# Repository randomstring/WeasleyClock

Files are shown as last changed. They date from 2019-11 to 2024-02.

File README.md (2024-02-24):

# Weasley Clock

Build a working physical [Weasley
Clock](https://harrypotter.fandom.com/wiki/Weasley_Clock) from Harry
Potter.

Photo album of the build: <https://photos.app.goo.gl/7yxiuzpsFReUh5Yy5>

Details of the build can be found in my [Build Log](BuildLog.md).

## Design

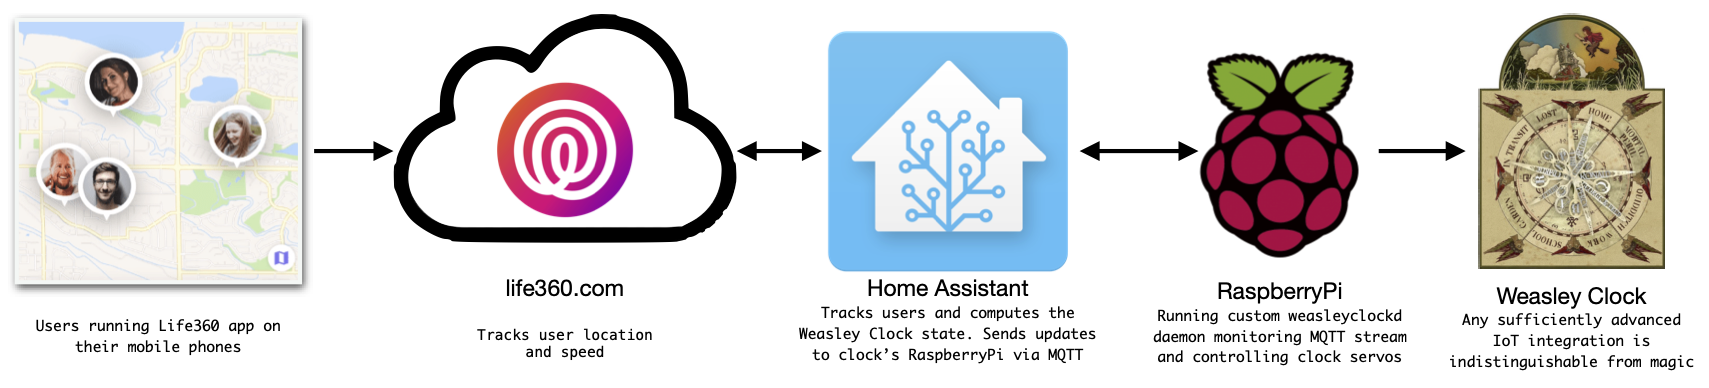
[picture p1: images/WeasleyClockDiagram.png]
Weasley Clock Flow Diagram


1. Track location of family members using the Apple iCloud integration
   in HomeAssistant. This service allows for real-time
   updates of each family member's location and speed. HomeAssistant allows
   for naming of arbitrary geo-fenced areas. This is used for labeling
   locations like school and work. I might switch over to using Traccar at some point to get
   better reporting on movement. The initial implementation used life360, but
   they locked out any external access to their API, breaking the HomeAssistant
   integration. 

2. Use [Home Assistant](https://www.home-assistant.io/) as a clearing
   house for family member location and movement within and around
   home. Home assistant is hosted on a Raspberry Pi
   running [Hass.io](https://www.home-assistant.io/hassio/).

3. Custom Home Assistant rules calculate the Weasley Clock state for
   each family member. Each state is visible from the Home Assistant
   dashboard. Changes in clock state are transmitted to the physical
   clock using the MQTT protocol over the network.

4. [Custom software](https://github.com/randomstring/weasleyclockd)
   running on a Raspberry Pi monitoring the MQTT message stream for
   changes in clock state and updating the physical clock hands to
   match. This software also adds some flare to hand movement. For
   example, the placement of the hand within each clock face sector
   will be determined by the person's distance from home. This way you
   can tell if someone is far or near to home at a glance. You might
   even be able to notice the progress of the person's clock hand
   progressing towards home.

5. A physical clock with four hands. The clock is mounted into an old
   grandfather clock. The face of the clock is divided into eight
   nearly equal sectors. Each sector has a location/situations
   label. These labels are: Home, Mortal Peril, Quidditch, Work,
   School, Garden, In Transit, and Lost.

6. The next phase will be to reuse the chimes that came with the
   original clock. The chimes can alert to noteworthy changes in the
   clock's state, for example, announcing someone's arrival back
   home. The current plan is to use a stepper motor to drive the
   existing chime mechanism.

## Clock Face and Meaning of Sectors

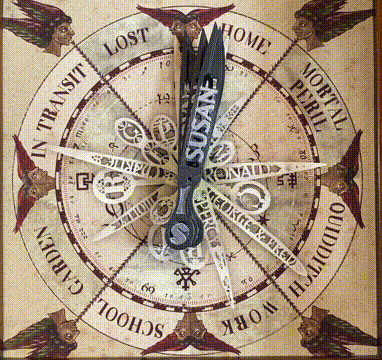
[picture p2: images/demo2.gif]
Weasley Clock Demo 2
Weasley Clock Demo 3 

What each sector of the clock face means:

* **Home** The home state is triggered by the Home Assistant Apple iCloud
  integration. I have a defined geo-fenced area, when we are inside
  that region, we are considered home. I also use the Home Assistant
  Unifi integration to identify when members of the family are
  connected to the home WiFi network. Additionally, I can identify
  which WiFi access points (APs) they are connected to. This provides
  some granularity as to where they on the property. The system can
  tell if someone is in the shop, in the main house, or outside in the
  garden. I use the clockwise half of the Home sector to indicate
  someone is in the main house and the counter-clockwise half to
  indicate someone is in the shop.

* **Lost** This is a catch-all state for when someone is stationary,
  not at home, and is not at one of the named locations of School or
  Work. The clock hand varies its location within the sector
  depending on how far from home they are. The closer to home, the
  closer the hand inches towards the Home sector. The position within
  the Lost sector varies on a logarithmic scale to give a finer
  grain detail when closer to home.

* **In Transit** This indicates the family member is on the move.

* **Garden** This sector is triggered when connecting to the WiFi
  access point outside, near the garden.

* **School** Triggered when at a location labeled as "school."

* **Work** Triggered when at a location labeled as "work."

* **Quidditch** Triggered when someone is bicycling. I have this
  triggered in two ways. First, by a complex set of rules about low
  speed movement, faster than walking and slower than
  driving. Secondly, I detect when someone is currently active on
  [Zwift](https://zwift.com/), an VR indoor cycling app.

* **Mortal Peril** This is triggered if the tracker measures someone's
  speed as greater than 75mph. With teenagers on the verge of driving
  age, I will be watching this one closely.

## Case Design

I decided to reuse an old grandfather/grandmother clock instead of
building a new case. I got lucky and found a perfect case at a thrift
shop. The clock was a petite grandfather clock, sometimes referred to
as a grandmother clock. Not as imposing and difficult to move as a
full sized grandfather clock. I needed the dimensions of the face to
match the artwork I have and the depth of the case needed to hold the
servos and new clockwork.

## Clock Hands

Hands are 3D printed with the name of each family member on the hands,
just like in the Harry Potter movies. The bottom of each hand has the
person's initial. Hands are painted for better contrast and to give an
aged appearance.

I spent a long time trying to figure out how to secure the hands to
the brass tube axles. I considered clamping hubs (too bulky), collets
(metal connectors traditional clock hands use), glue, and hot glue
(this works well). In the end, by making the holes in the 3D printed
hands strategical smaller, I was able to expand the holes with a file
so that they just fit. They were tight enough to be secure. I did
remove too much material from one of the hands and resorted to glue
(E-6000) to keep it in place.

Here are the [fonts](fonts/Fonts.md) I evaluated for use on the hands.

## Related Projects and Inspiration

Over the course of this build I spent a fair amount of time
researching how others have attempted to build a Weasley Clock. The
most complete and authentic build I've found is by [Printable
Props](https://www.instagram.com/printableprops/).

-   <https://www.allderhallows.com/>
-   <https://hunterjm.github.io/location-clock/>
-   <https://github.com/WhereslyClock/MyWhereslyClock>
-   <http://www.themagicclock.com/>
-   <https://printableprops.jimdo.com/en/harry-potter/weasley-clock/>
-   <https://www.instructables.com/id/Build-Your-Own-Weasley-Location-Clock/>
-   <https://www.facebook.com/PrintableProps/>
-   <https://www.instagram.com/printableprops/>
-   <https://fourierinformationsir.wordpress.com/2015/11/09/weasley-clock-update/>
-   <https://twitter.com/wbtourlondon/status/765398939910627328>
-   <https://www.youtube.com/playlist?list=PL86twtxo_L9TMY4A5TcG2nJcsyFx2CWhb>
-   <https://magicclock.de/>
-   <http://www.brettoliver.org.uk/Longcase_Clock/Longcase_Clock.htm>
-   <https://www.youtube.com/watch?v=NH0jhxouQM8>
-   <https://www.youtube.com/watch?v=WJ2PBmOW_Rc>
-   <http://www.thisispete.com/work/prototyping/weather_clock/>
-   <https://imgur.com/gallery/wX98fOc>
-   <https://www.reddit.com/r/homeassistant/comments/ts0y6a/got_round_to_converting_my_weasley_clock_to_be/>

## Artwork

I looked around on the internet and there are two styles of faces for
the Weasley clock that appear in the Harry Potter movies. The first
style comes up more often, and it is easier to replicate. It also has
some sectors like "Prison" that I hope to never need.

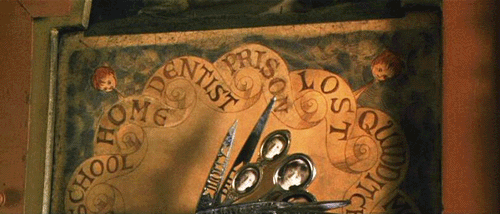
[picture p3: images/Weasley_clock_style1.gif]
Weasley Clock Style 1


I prefer the second style.

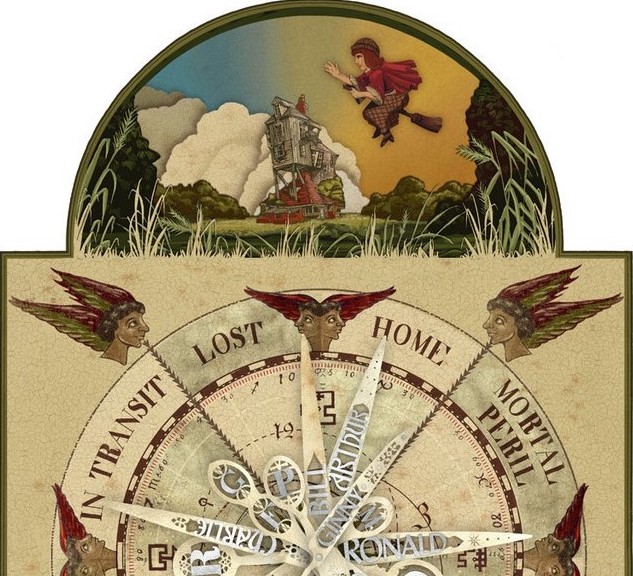
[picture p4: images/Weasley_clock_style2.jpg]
Weasley Clock Style 1


As luck would have it, [Minalima](https://minalima.com/), the artists
of this style, sell officially licensed [posters of the Weasley
Clock](https://minalima.com/product/the-weasley-family-clock/). This
was well worth the money for the poster as I didn't have to create the
artwork myself and this *is* the artwork from the Harry Potter movie.

## Chimes

The grandmother/grandfather clock came with a set of chimes. I plan to
integrate them once I have the clock mechanism finished. I started a new project to research and document this build: [Weasley Chimes](https://github.com/randomstring/WeasleyChimes/).

## Home Assistant

I am using [Home Assistant](<https://www.home-assistant.io/>) for
tracking and transmitting the location of my family members. To do
this I am using the [Apple iCloud
integration](<https://www.home-assistant.io/integrations/icloud/>) for
detailed location tracking. For tracking finer locations around the
house I am using the [Unifi
integration](<https://www.home-assistant.io/integrations/unifi>) to
monitor which WiFi access point each family member is closest to.

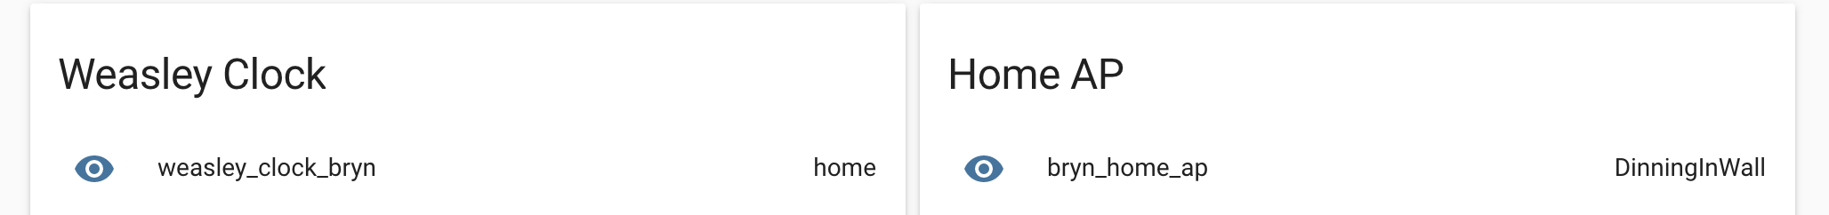
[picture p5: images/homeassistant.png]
Home Assistant Weasley Clock


I'm including example Home Assistant YAML configuration code creating
a Weasley Clock sensor. This sensor will track a given user's Weasley
Clock states:  home, garden, school, work, intransit, mortalperil, lost, error.

Example Home Assistant configurations can be found in the
homeassistant directory. 
 * [automations.yaml](homeassistant/automations.yaml)
 * [sensors.yaml](homeassistant/sensors.yaml)

## Software

I need a daemon running on the Raspberry Pi that controls the clock
servos. For this I
wrote [weasleyclockd](https://github.com/randomstring/weasleyclockd)
that monitors the MQTT messages from Home Assistant and manages the
physical clock movement.

## CAD Models of Parts

Most of the parts from ServoCity.com have CAD models that can be found
here: <https://www.servocity.com/step-files>

CAD model of the HS-785HB Servo can be found here:
<https://grabcad.com/library/servo-motor-hitec-hs-785hb-1>

Custom CAD files for the clock supports and hands are in the
[CAD](CAD) sub-directory. 

The CAD for the clockworks support structures were created by my
father-in-law, Ron. He also handled all the 3D printing for this
project.

My son, Alex, did the CAD for the clock hands, and generated a CAD
rendering of the clockworks. Complete [CAD renderings of the clockworks
and hands are on GrabCad.com](https://grabcad.com/library/weasley-clock-2).

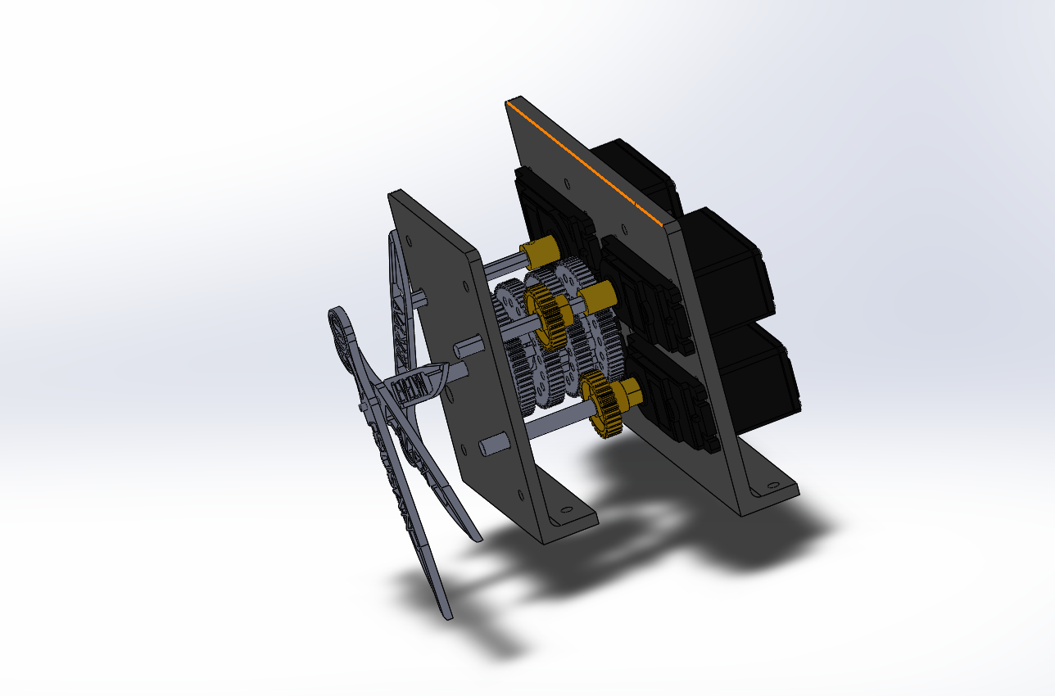
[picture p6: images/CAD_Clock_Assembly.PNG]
Cad View

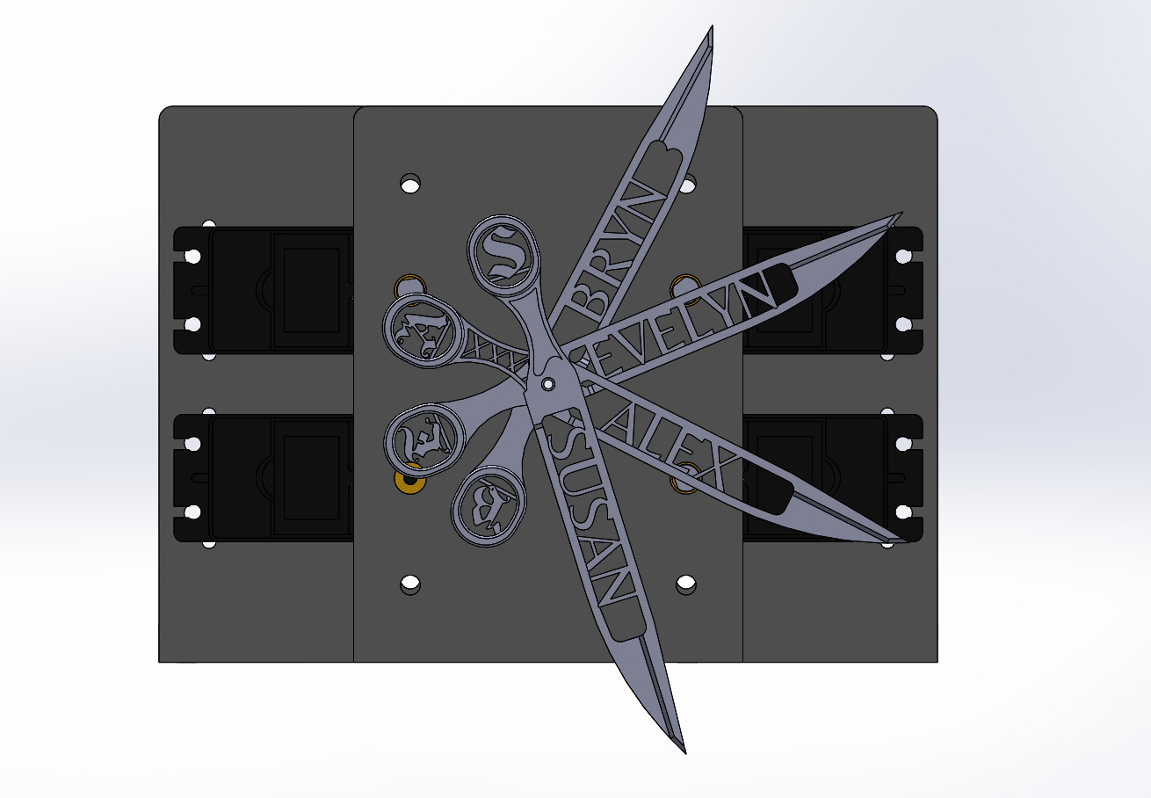
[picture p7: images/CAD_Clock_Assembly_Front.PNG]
CAD Front View


## Mounting poster to plywood

I used 3M Super 77 Spray Adhesive for mounting the clock face artwork. 

I had considered using [Mod
Podge](https://www.amazon.com/Mod-Podge-CS11303-Waterbase-Sealer/dp/B0009ILH8C/)
and went so far as experiment mounting some other posters to plywood
using Mod Podge. 

3M Super 77 leaves the face surface smoother, and doesn't require
coating the front of the art to get good adhesion. Super 77 sets up
really quickly, so watch some videos on how to use it and get a buddy
to help keep the poster straight as you lay it down.

# Shopping list

## Raspberry Pi

-   standard set of Raspberry pi requirements. Pi, power supply, SD card, case

## Servo Hat

-   Raspberry Pi servo hat: <https://www.adafruit.com/product/2327>
    -   requires soldering
-   Servo power, one of:
    -   5V 2A should be enough if motors aren't overloaded simultaneously <https://www.adafruit.com/product/276>
    -   5V 4A to hedge bets, or if you run more servos <https://www.adafruit.com/product/1466>

## Shopping list from Servo City

<table border="2" cellspacing="0" cellpadding="6" rules="groups" frame="hsides">

<colgroup>
<col  class="right" />

<col  class="left" />

<col  class="right" />
</colgroup>
<thead>
<tr>
<th scope="col" class="right">Count</th>
<th scope="col" class="left">Description</th>
<th scope="col" class="right">SKU</th>
</tr>
</thead>

<tbody>
<tr>
<td class="right">4</td>
<td class="left">HS-785HB SERVO</td>
<td class="right">33785S</td>
</tr>

<tr>
<td class="right">3</td>
<td class="left">32T, 0.250" (1/4) Bore 32P Shaft Mount Pinion Gear</td>
<td class="right">615254</td>
</tr>

<tr>
<td class="right">1</td>
<td class="left">32P, 32 Tooth, 24T C1 Spline Servo Mount Gear (Metal)</td>
<td class="right">615290</td>
</tr>

<tr>
<td class="right">3</td>
<td class="left">C1 SPLINE SERVO TO 1/4" SHAFT COUPLER (SET SCREW)</td>
<td class="right">525134</td>
</tr>

<tr>
<td class="right">3</td>
<td class="left">0.250" (1/4") X 2.50" (2-1/2") STAINLESS STEEL D-SHAFTING</td>
<td class="right">634074</td>
</tr>

<tr>
<td class="right">4</td>
<td class="left">32 Pitch, 64 Tooth (.50" Bore) Aluminum Hub Gear</td>
<td class="right">615194</td>
</tr>

<tr>
<td class="right">2</td>
<td class="left">6mm (0.770") Clamping Hub</td>
<td class="right">545616</td>
</tr>

<tr>
<td class="right">2</td>
<td class="left">5mm (0.770") Clamping Hub</td>
<td class="right">545612</td>
</tr>

<tr>
<td class="right">2</td>
<td class="left">4MM (0.770") Clamping Hub</td>
<td class="right">545608</td>
</tr>

<tr>
<td class="right">2</td>
<td class="left">3MM (0.770") Clamping Hub</td>
<td class="right">545604</td>
</tr>
</tbody>
</table>

## Shopping list from Hobbylinc

-   <https://www.hobbylinc.com/htm/k+s/k+s9821.htm>
-   NOTE: checked items are a good set for a 4 hand clock. Theoretically
    possible to create a 6 hand clock with all of the sizes. However,
    servocity doesn't sell clamping hubs for size 2mm and 7mm.
-   parts:
    -   [ ] 2mm x 300mm Round Brass Tube .45mm Wall (4) k+s9820 Item # K+S9820
    -   [X] 3mm x 300mm Round Brass Tube .45mm Wall (4) k+s9821 Item # K+S9821
    -   [X] 4mm x 300mm Round Brass Tube .45mm Wall (3) k+s9822 Item # K+S9822
    -   [X] 5mm x 300mm Round Brass Tube .45mm Wall (3) k+s9823 Item # K+S9823
    -   [X] 6mm x 300mm Round Brass Tube .45mm Wall (2) k+s9824 Item # K+S9824
    -   [ ] 7mm x 300mm Round Brass Tube .45mm Wall (2) k+s9825 Item # K+S9825

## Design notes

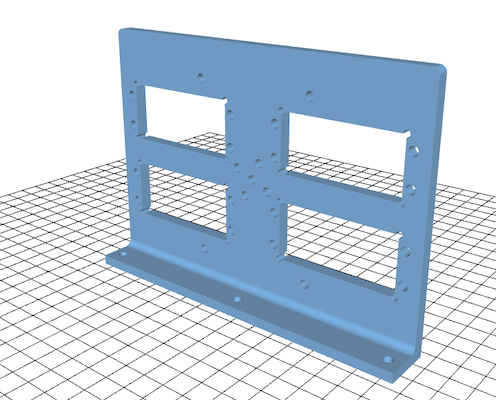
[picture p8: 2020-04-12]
images/CAD_servo_support.png

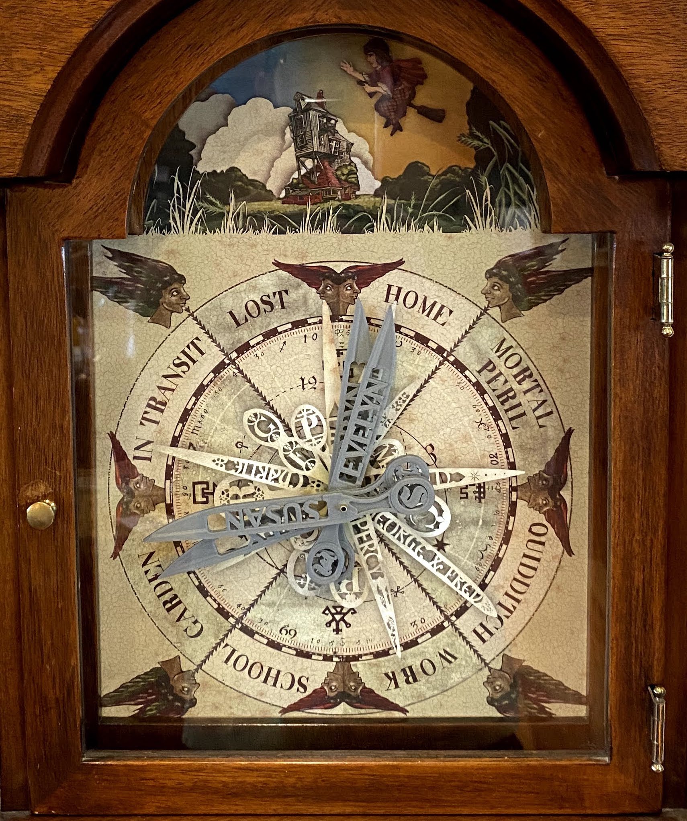
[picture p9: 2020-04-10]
images/WeasleyClockFace.jpeg

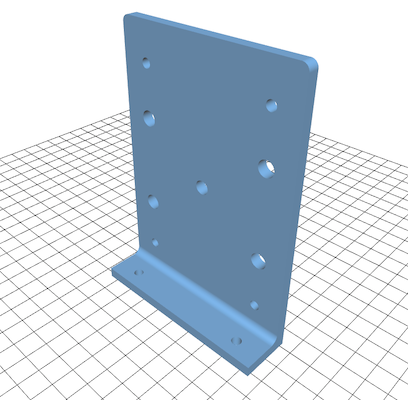
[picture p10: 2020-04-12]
images/CAD_shaft_support.png

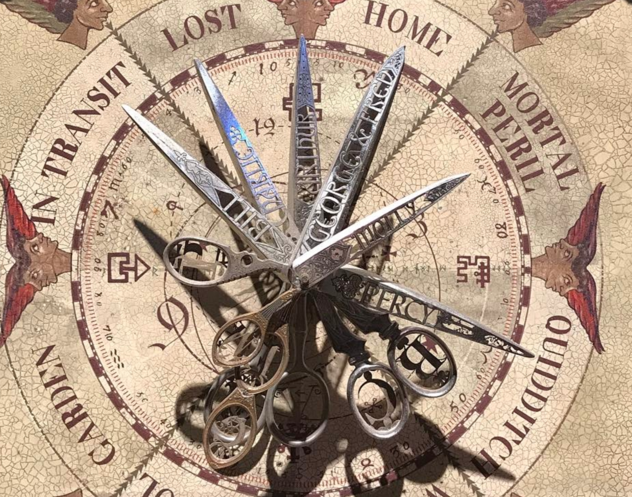
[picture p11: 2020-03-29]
images/ClockHands.png

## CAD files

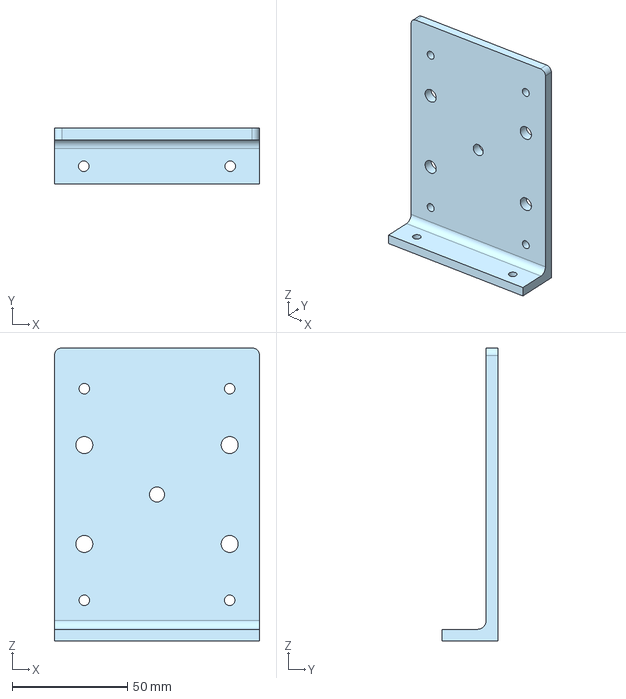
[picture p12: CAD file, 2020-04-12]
CAD/Clock_Shaft_Support.step
88.9 x 24.1 x 127.0 mm

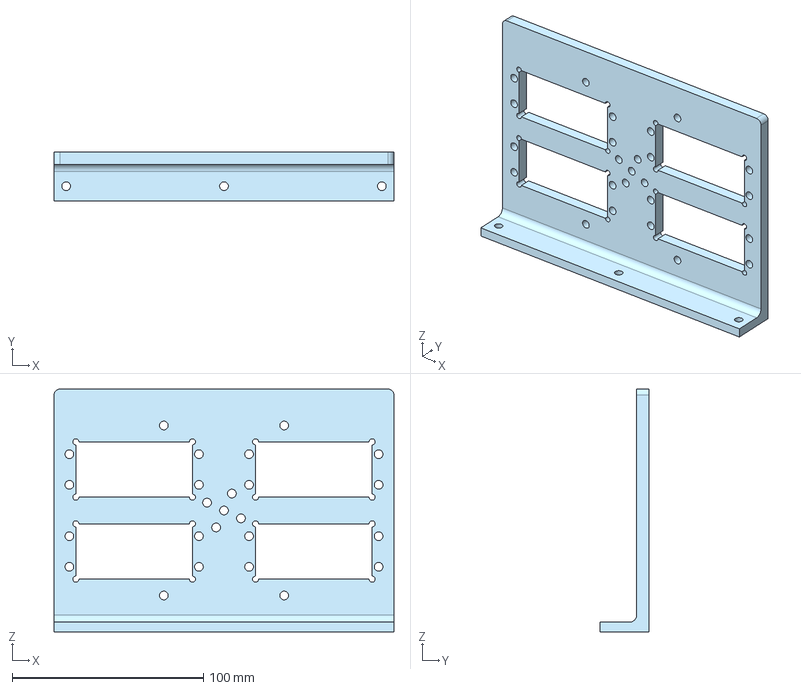
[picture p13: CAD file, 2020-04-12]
CAD/Clock_Servo_Support.step
177.8 x 25.4 x 127.0 mm

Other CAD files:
CAD/Clock_Servo_Support.stl
CAD/Clock_Shaft_Support.stl

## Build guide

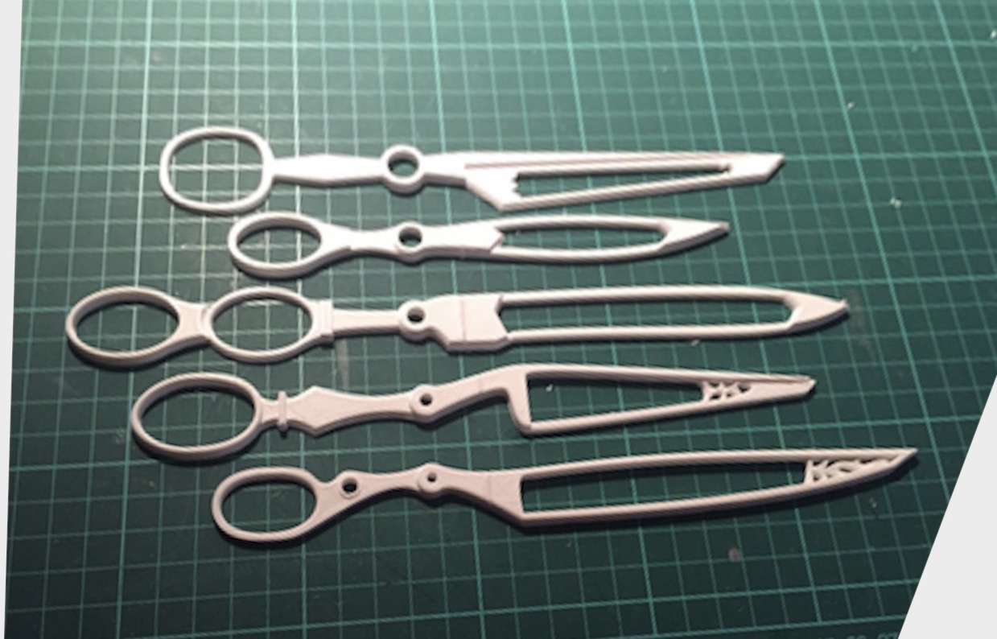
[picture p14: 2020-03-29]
images/PrintableProps_Hands.jpg

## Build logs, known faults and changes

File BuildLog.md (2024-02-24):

# Build Log

I started this log after getting the Weasley Clock feature complete. I
should have started from the beginning. Entries prior to April 2020
are written retrospectively.

## TODO: Build/Code

* create code/algorithm to reliably detect when people are bicycling for the Quidditch state
* better document Zwift integration, post example home assistant configuration

## Why Home Assistant?

I started using [Home Assistant](https://www.home-assistant.io/) when
I was looking at home automation choices. What started this was my
purchase from [Konnected](https://konnected.io/), a system that
converts an old wired alarm system to a modern IoT integration.

Home Assistant is open source and strives to keep all control local
(and private) to your home network.

After over a year of tinkering with Home Assistant, I feel like I've
only scratched the surface of what it's capable of.

I published [example configuration
templates](https://github.com/randomstring/WeasleyClock/tree/master/homeassistant)
for integrating into Home Assistant.

## Why Life360?

I tried the Home Assistant Apple iCloud integration first. The iCloud
API does not seem to be a fully supported and endorsed API. The Home
Assistant integration broke for me at least twice. Once when Apple
changed some details in their authentication.

The Life360 integration has been quite stable and has features
designed around tracking family members. I also managed to get buy-in
from all my family members to use it. Which makes all of this possible. 

Another point is that it works on both iPhones and Android phones.

Life360 allows for setting up several geo-fenced regions and giving
them labels. For instance I have a geo-fence region for each school.
Home Assistant also has this feature, so this can be done in Home
Assistant just using the latitude and longitude provided by Life360.

## Why MQTT?

MQTT is fairly easy to use, can generate arbitrary messages (I use
JSON for the payload), and has extensive support in Home Assistant.

Using python the [Paho MQTT](https://pypi.org/project/paho-mqtt/)
module.

I implemented the MQTT the Weasley Clock Server/Client in a stand
alone repo called
[weasleyclockd](https://github.com/randomstring/weasleyclockd).

The other obvious choice would have been to use an HTTP and RESTful
API. I haven't ruled out adding one. 

## Monolithic Approach

Alternatively, I could have just implemented a direct integration with
Life360 on the Raspberry Pi. This would have taken the form of a
single daemon running on the Weasley Clock that would poll Life360 and
do all the state calculations.

This would have been less complicated, removing the need for Home
Assistant and the MQTT broker. There are a couple downsides to this
approach. First, I would need to keep the Life360 API up to date in the
event the API or the authentication scheme changed. If Life360 goes
away for some reason, I can switch to some other location tracking
system supported by Home Assistant. Secondly, I can leverage the Unifi
Home Assistant integration to track which Wi-Fi AP people are connected
to. AP level locations allow figuring out when someone is in the Shop
or outside in the Garden.

## Clock Body Details

I reused the original wood where possible to keep the aged look of the
clock. When I needed to use new wood I stained it to match.

I tried to use as much brass hardware as possible.

## Why Servos ? What other options?

I used servos, because when I was looking at rotational control, this
was what I found ready made solutions for first. I found  multi
rotation "sail" servos and the Pi Servo HAT solution first.

Since then I've done some programming on robots. I think a motor with
an encoder to track the location would be a better solution. The
position control could be more precise and it would give the option of
using PID and motion profiling to customize the hand movement.

Maybe I'll make another version of the clockwork using motors and
encoders.

A third option would be to use stepper motors. I purchased a raspberry
pi motor controller hat to test controlling stepper motors.

Below are some seeds for future research. 

I found this possible motor and encoder combination:
<https://wiki.dfrobot.com/DC_Motor_Driver_HAT_SKU_DFR059>
<https://wiki.dfrobot.com/12V_DC_Motor_122_rpm_w_Encoder_SKU__FIT0403>

Another encoder option:
<https://www.youtube.com/watch?v=RLCPKa9SoF0>
<https://www.superdroidrobots.com/shop/item.aspx/quadruple-ls7366r-quadrature-encoder-buffer/2418/>

Stepper motor with encoder:
<https://www.digikey.com/product-detail/en/cui-devices/NEMA14-10-04D-AMT112S/102-4710-ND/9477637>

Possible motor from ServoCity.com:
<https://www.servocity.com/76-rpm-spur-gear-motor-w-encoder>
<https://www.servocity.com/encoder-breakout-cable-4-pos-jst-xh-mh-fc-to-4-x-1-pos-tjc8-fh-mc-300mm-length>

## Notes on parts

-   <https://www.servocity.com/32p-24t-c1-spline-servo-mount-gears-metal>
    NOTE: The 32 tooth gears don't fully clear the servo body. This
    means that to use more than one servo, we need to use a shaft so
    that central 64 tooth gears don't hit/interfere with the servos.
-   Using 64 tooth gears mounted to the brass tubes. This gives a clean
    1:2 ration from the servos.
-   HS-785HB Servo
    -   specs <https://www.robotshop.com/media/files/pdf/hs-785hb.pdf>
    -   Grabcad model <https://grabcad.com/library/hitec-hs-785hb-winch-servo-1>
    -   The HS-785HB Servos have a claimed 8 full rotations. I only need
        2 full rotations to get the full range of motion of the clock
        hands. Having more than 360 degrees of motion allows for a little
        **flair** when positioning the hands. I'm going to use just 6 full
        rotations of the servo (so 3 full rotations of the hands) to
        avoid using the extremes of the PWM signals to the servos.
    -   Stall current for HS-785HB is 1500mA. Max current 6A (at 5V?)
    -   No load current for HS-785HB is 230mA
    -   Idle current for HS-785HB is 9mA
-   possible screws for attaching to clamping hubs? 6-32
    -   SKU 91771A145  length 0.3125" (5/16")  <  0.333" = 0.25" (hub width) + 0.083" (screw head depth)
    -   <https://www.servocity.com/6-32-flat-head-phillips-machine-screws>

## Why only 4 hands?

When I first conceived of the idea, I expected to find a number of
commercial multi-hand clockworks to choose from. There are plenty of 3
hand clocks out there (hour, minute, seconds) and some are kits that
would be hackable. I did not find any 4 or more clock hand solutions.

Four was the minimum number I needed, as that was the size of my
immediate family. I wanted to do more, ideally 7. That posed several
problems. I was able to find a set of 7 consecutive nesting brass
tubes 2, 3, 4, 5, 6, 7, and 8 mm. However I could not find clamping
hubs in for 2mm, or 7mm sizes. Another challenge was fitting more than
4 servos around the central shaft. Finally, the depth of the clockwork
would be almost double, making fitting it into a case more difficult.

These are just problems to be overcome. 

# Diary

## 2019-02-07 Pi Servo HAT

Ordered the [Adafruit 16-Channel PWM / Servo HAT for Raspberry
Pi](https://www.adafruit.com/product/2327) to start experimenting with
running servos. 

The servo HAT requires soldering on the headers. I watched a few
YouTube videos like this one to learn how
<https://www.youtube.com/watch?v=t9LOtOBOTb0> 

I got the larger capacity [5V 4A (4000mA) switching power
supply](https://www.adafruit.com/product/1466) that can power more
servos. This 4 Amps, might be overkill but at the time I didn't know
which and how many servos I would need to drive.

## 2019-03-07 Brass Tubes

Order a set of nesting brass tubes from Hobbylinc. I order them in
metric whole millimeter sizes. The wall thickness on each is .45mm,
leaving 0.1mm of clearance for the next smaller size of tube.

Here is a link to the 4m size tube:
<http://www.hobbylinc.com/htm/k+s/k+s9822.htm>

I also get mounting hubs for attaching gears to the hubs
<https://www.servocity.com/770-clamping-hubs>.

## 2019-03-13 Order Servos and Gears

Made my first order from [Servo City](https://www.servocity.com/) for
a multi-turn "sail winch servo." Specifically the [HS
785hb](https://www.servocity.com/hs-785hb-servo) This is a servo that
has a range of motion more than 360 degrees. Most servos have a range
of less than 360 degree. 

I talk about other options for accurate rotation of for the clock
hands, but at this point I had done enough research to know this
should work.

## 2019-03-14 Thinking about Hands

So I'd been thinking about how I was going to design, make, and
ultimately attach clock hands. Of all the similar projects I found, by
far the best was by [Printable
Props](https://printableprops.jimdofree.com/en/harry-potter/weasley-clock/). I
messaged the creator, Pascal, hoping he might share the CAD for his
clock hands. He went full on authentic, artistically re-creating the
hands from the movie. Sadly I didn't hear back. 

My friend Ben suggested outsourcing the hands to
[Shapeways](https://www.shapeways.com/). I came pretty close to doing
that.

Thankfully, my son was enrolled in CAD and Advanced CAD at his high
school. By the time I really needed the hands done, he was able to use
his mad CAD skills to create custom hands in SolidWorks.

## 2019-06-19 Prototype Clockworks

I build the first prototype of the clockworks and some [custom code to
control the HS 785hb
servos](https://github.com/randomstring/weasleyclockd/blob/master/hs785hb_servo.py).

## 2019-10-24 Thrift Store Gold!

I had been thinking (and worrying) about how I was going to enclose
the Weasley Clock. I was thinking of building a custom housing for it
and mount it to the wall. This would have required improving my crude
woodworking skills.

Then I spotted this Grandfather clock in a thrift store in Langley,
Washington. I had actually spotted this exact clock three months prior
on a visit to Whidbey Island. At the time, I didn't have the
measurements for the artwork and no way to tell if everything would
fit. I was also traveling with my wife, for whom the clock was a
surprise present, so I chose to be discrete and not start measuring the
clock on the spot.

Upon returning home, I measure the clockwork and artwork so I could
identify old clocks that would fit. I did some searching on eBay.com
for possible candidates, however working clocks were expensive and
virtually all could not be shipped. Finding the perfect clock in
Florida available for pick up only wasn't an option.

Fate had me returning to Langley three months later and I went straight
to the thrift shop. The clock was still there, and the price had come
down $85. A few quick measurements later and I was positive I had a
good fit.

My wife was curious at my need to purchase the clock, but kept her
curiosity in check as she knew it had something to with a surprise for
her.

Grandmother clock by Colonial MFG Co, Model 1866 $165 in a thrift store.

## 2020-02-20 Plug It In

The pi and servos need power. The servos have their own power supply,
so I needed at least two outlets inside the clock to provide power. I
found this extension cord
<https://www.amazon.com/gp/product/B07BBGM5WH/> on Amazon. That fit
with my sense of aesthetics for the clock. And because it was a dark
gray, it's almost invisible inside the base of the clock. I also
purchased a black pi USB power
supply. <https://www.amazon.com/gp/product/B00MARDJZ4/>

I drilled a hole in the bottom of the clock big enough for the cable
and then voided the warranty on the cord by cutting it, feeding the
cable through and then splicing it back together. I didn't want to
make a huge hole to squeeze the plug through.

I ran the pair of black power cables for the pi and servos up the
back, inside corner of the case. They are discreet enough that you
don't see them, unless you're looking for them.

## 2020-04-01 Magic Wands

Had the thought that I could create a replica Harry Potter magic wand
with a strong magnet in the tip and install a few magnetic reed
switches inside the clock. I could then pull out the want and tap the
clock to trigger events. This would be a cool way to trigger a `Demo
Mode`.

## 2020-04-04 MOTD

Added a Harry Potter Themed message of the day.

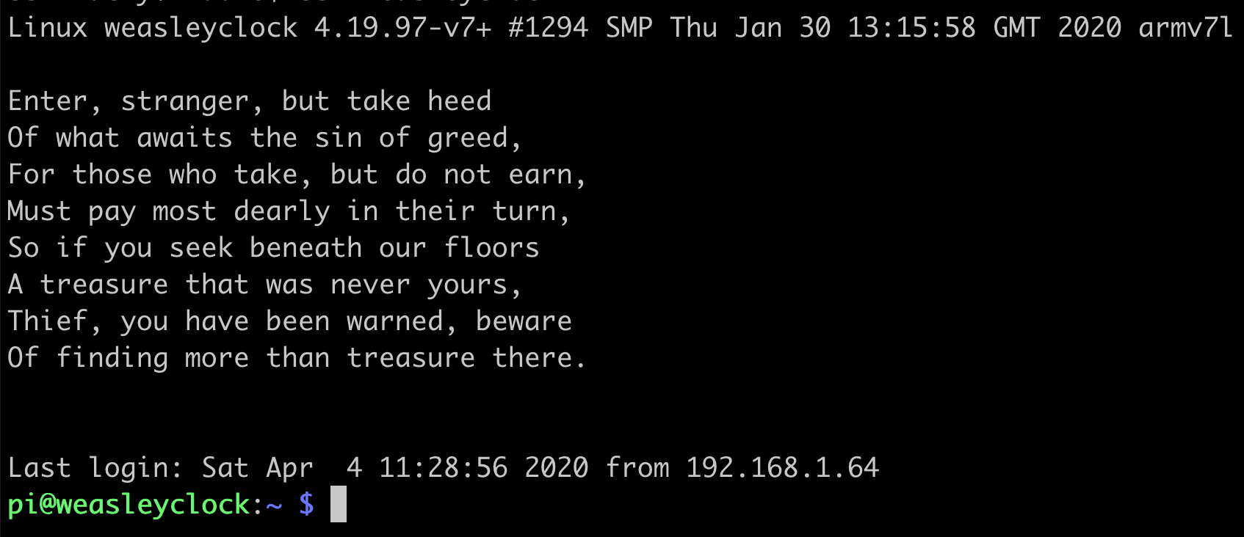
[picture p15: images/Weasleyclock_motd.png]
Message of the day


## 2020-04-05 Feature Complete!

Thanks to my son's CAD design work for the clock hands, I now have a
fully working Weasley clock. The clock is now installed in the kitchen.

## 2020-04-06 Make Garden Accurate

Because the WiFi Access Point that I have reserved for outside is
still inside near the front door, the clock will oscillate a person
between `Garden` and `Home` if they walk through the front of the
house. I needed to install the AP outside, near the garden. I've been
putting this off as it wasn't on the critical path, until now.

Today I got up on a ladder and installed the Unifi AP AC Pro outside
near the garden. I thought that the AP AC Pro had pass-through POE, so
I stole the POE connection for one of the Unifi G3 POE cameras to run
the AP. Then I just daisy chained the G3 camera to the AP. Turns out,
it's just a regular Ethernet port, no POE. I'll need to run another
Cat6 cable to get the camera running again.

Also started a new project on GitHub to [operate the grandfather clock
chimes](https://github.com/randomstring/WeasleyChimes).

## 2020-04-07 More Cat6, MQTT Scripting

Ran another Cat 6 cable to power the Unifi G3 camera. I managed to get
the custom Cat 6 cable crimped correctly on the first try. One
Ethernet jack was crimped while standing on a ladder. #winning

Started writing `mqtt_script.py` a python program to send a scripted
sequence of MQTT messages. I plan to use this to create demonstrations
of what the Weasley Clock can do. The script should have other uses as
well since it is not project specific and can send arbitrary MQTT
messages.

## 2020-04-09 Zwift Integration & Documentation

Added the [Zwift](https://zwift.com/) integration to Home Assistant
<https://pypi.org/project/zwift-client/>. This required installing the
[HACS](https://hacs.xyz/) community software store to Home
Assistant. I need to look at HACS some more to see about adding and
testing my own features.

The clock now registers me in the state Quidditch whenever I'm
actively riding on Zwift.

Worked on cleaning up documentation.

## 2020-04-11 Diagram

Spent the morning creating a pretty flow diagram for README.md.

Researched quadrature encoders for the raspberry pi.

## 2020-04-12 CAD

Add clock support CAD files. Remove ServoCity.com library CAD files,
as they are hosted at <https://www.servocity.com/step-files>.

## 2020-04-16 Painting and CAD

I spent the last few days experimenting with painting the clock
hands. The recipe I like is to clean up the 3D printed piece. Smooth
it with a file and then emery paper. Next a layer of primer to help
give it a smooth surface. Then paint with metallic nickle spray
paint. Then mask off the letters of the name with blue painters
tape. Then finish with a light, approximately 75% coverage of the hand
with flat black paint. This lets a bit of the silver nickle shine
through, but provides good contrast against the clock face. Final
step is to remove the masking tape to reveal the names in bright
silvery metallic nickle.

Now I need to remove the hands from the clock, paint the hands, and
then re-install them.

I hired my son to create CAD files in SolidWorks of example clock
hands with the Weasley family names from the Harry Potter movies. He
also created a CAD rendering of the clockwork.

I need to get those uploaded to GitHub and to Grabcad.

## 2020-04-17 Repaint

Removed the 3D printed hands from the clock and started painting
them. First primer coat applied.

## 2020-04-25 Finished painting

Finished painting and reinstalled. Back up and running! With COVID-19,
there isn't much movement other than people moving between "Home" and
"Garden."

## 2020-04-26

Worked on the MQTT script replay program to be able to demo various
features. In the process the MQTT broker on my Home Assistant went a
little wonky, I discovered that the broker I had installed was now
deprecated, migrated to the supported MQTT HA broker, and in the
process had no working MQTT for most of a day. It's all working now.

Turns out port 4883 is a non-standard MQTT over SSL port. Switched to
using port 8883.

Fine tuning
[demo2](https://github.com/randomstring/weasleyclockd/blob/master/demos/demo2.json)
to demonstrate what happens when someone is far from home and then
travels back home.

## 2020-05-01

Figured out why the hand placement was off for some of the edges of
some segments. I only just noticed that the the clock segments on the
artwork are not all equally sized. I had assumed that all 8 segments
were equal size and thus 45deg wide. Instead half of the segments are
40 degrees and half are 50 degrees. 

## 2020-05-05

Demo work. Improved demo scripts. Filmed stable video of demos. Made
animated GIFs of demos.

```
 ffmpeg -i IMG_7587.MOV -vf crop=1146:1080:387:0,scale=382:360,fps=6 demo2.gif
 ffmpeg -i IMG_7586.MOV -vf crop=1146:1080:387:0,scale=382:360,fps=6 demo3.gif
```

## 2020-05-10 

I just found <http://www.themagicclock.com/>. This person made many of
the same decisions I did, including using sail winch servos and
reusing an antique clock body. No location tracking, or at least not
when they last updated their webpage.

## 2020-05-17 3D Printed Gear Research

Shopping around for alternate build options. 

Not sure why I overlooked McMaster-Carr in the past.
https://www.mcmaster.com/shafts/copper-brass-and-bronze/system-of-measurement~metric/shape~round-tube/

Customizable Shaft Collar
https://www.thingiverse.com/thing:3694236

Examples of 3D printed shaft connectors.
https://howtomechatronics.com/projects/arduino-3d-wire-bending-machine/
https://howtomechatronics.com/projects/arduino-mecanum-wheels-robot/

3D printed motor mount and gears
http://lukemetz.com/mechanical-v2-base/

Quora Ideas on how to attach 3D printed gears to metal shafts
https://www.quora.com/What-is-the-best-way-to-secure-a-3D-printed-PLA-gear-to-a-metal-shaft

## 2020-05-19

Wrote a blog post about the project, focused more on the non-technical side. https://randomstring2.blogspot.com/2020/05/weasley-location-clock-project.html It's been 5 years since my last blog post. Given how terrible blogger is, it might be another 5 before the next one. 

This project got onto the Hacker News front page. It got as high as #12 (that I saw). https://news.ycombinator.com/item?id=23235807 Woot!

## 2020-06-01 Detect when Bicycling

This had been bothering me for a while. The Life360 moving state would
be too easy to confusing with driving or even walking. I could use a
range of speed that I assigned to be cycling. However, this would
require implementing an average speed sensor. Even with the average
speed, there are situations when I might be driving slowly (stuck in
traffic) or biking quickly (down a long descent) that would be outside
any fixed range. I could use geolocation to get street names and
figure out when I'm on a bike train or an interstate and set the
activity accordingly. I looked into ways to detect what device my
phone was paired with via Bluetooth. If my phone was paired with my
Garmin cycling computer, I would know I was cycling. I was starting to
think I was going to have to write a complicated state machine as a
custom plugin or script to make a reasonable guess at when I was
biking or not. This is why I was procrastinating this task...

In the end I took one last look at the Garmin LiveTrack feature. This
will send an email with a URL for tracking your ride in real time. I
use this email as a trigger when I start a ride and I use my return
home as a trigger that the ride is over. In the future I'll work on
actually pulling the URL from the email to detect when the ride is
over. Or just time out after 2 hours of being stationary.

Steps:
 - create a dummy gmail account to receive notifications
 - turn on LiveTracking on my Garmin 530 and send notifications to new gmail account
 - enable email sensor on HA https://www.home-assistant.io/integrations/imap_email_content/
 - autoarchive new emails after 15 minutes
   see: https://medium.com/@fw3d/auto-archive-emails-in-gmail-after-2-days-1ebf0e076b1c
 - email sensor look for start of LiveTrack email, this signals start of ride
 - autoArchive script removes email after 15 min
 - end of ride when returning home

Still to do is to flag the end of the ride even when not at home. This
can be done by following the LiveTrack URL and monitor when the ride
is actually over. Would be nice if there were an API.

Strava used to have API access to the Strava Beacon feature, but it
seems to be gone in the current API version.

Alternatively, I can manually send an email to flag the end of a ride.

# 2020-06-11

Purchased a Wahoo ROAM bike computer. The Wahoo Fitness live track
feature has a permanent URL so I can monitor a single URL to detect
when I start and stop biking. Still need to write code to check the
URL and parse out the biking state.

Garmin sucks, so this was a welcome motivation to make the switch to
Wahoo. Wahoo also has a cloud API in the works. 

# 2020-06-13

Noticed that clock state sensor in HomeAssistant was not getting
updated often enough. Only on major state transitions 'moving' to
'stationary' for instance. I added the home assistant proximity
integration to add something with a value that would change as the
person moved. I used meters as units so that even small movements
would trigger a weasleyclock state update.

# 2020-07-16

This WeasleyClock project was included in the [GitHub Archive
Program](https://archiveprogram.github.com/). Now when aliens unearth
the wreckage of human civilization, they'll have instructions on how
to build a WeasleyClock!

# 2020-07-30

This project got written up on Hackaday
<https://hackaday.com/2020/07/29/do-you-know-where-your-children-are-check-the-weasley-clock/>

# 2020-07-31

This project got written up on Tom's Hardware
<https://www.tomshardware.com/news/raspberry-pi-weasley-family-clock-from-harry-potter-runs-like-magic>

and made Tom's Hardware list of best Pi projects for August 2020:
<https://www.tomshardware.com/amp/features/best-raspberry-pi-projects>

Made a first attempt at coding the Quiddich state detector using the
iOS activity sensor. On iOS each activity has it's own state, true or
false. However, the way that the Home Assistant app reports it is as a
single state, and cycling is at the bottom of the reporting. So if
Walking, Running, or driving is set to true, the Cycling state is
never set. So I'm considering Walking and Running to be cycling if the
speed is greater than 12 mph.

I'm moving away from Garmin and today my email quidditch trigger took
almost an hour to get delivered. This new detector should be more
robust and it does not require any action on my part to trigger the
Quidditch state.

# 2020-09-06 Queue state changes

So after living with the clock for a while some states can flip back
and forth pretty quickly, especially between the Garden and Home
states. These states are triggered by that person's phone connecting
to different Wi-Fi access points and susceptible to the mysteries of
wifi AP assignment. For instance, walking into the garage would
sometimes trigger the Garden state. Worse, when near the house your
phone might keep jumping between two APs (outside and inside) and the
clock would just go nuts, swinging your clock hand back and forth
between Garden and Home.

My solution was to put a 30 second delay before moving the clock hands
for certain states: Home, Garden, and Barn. This should cut down on
some of the flailing. This is not perfect, and I should implement a
proper queue.

I made a second improvement to the staggered hand style. This style is
now adaptive to how many hands were in that sector. If there's just
one person in the Garden, that hand is right in the middle of the
sector. If a second person goes into the garden that hand moves over
to make room for the other hand. Likewise for 3 and 4 hands in the
same sector. This gives the hand movement a more organic feel as the
hands in the target sector move slightly as a new hand moves into the
sector.

After six months one of the hands occasionally squeaks. I didn't put
any lubrication in the shafts or on the gears and I'm probably going
to have to take it all apart and apply grease sometime soon.

## 2021-06-19 WhereslyClock

This project inspired a new Weasley Clock project
<https://github.com/WhereslyClock/MyWhereslyClock> using Arduino,
MQTT, and C. This is a lower budget build using more 3D printed parts
and less expensive motors. Nicely done!

## 2021-07-02 Wahoo Live Updates

I was hoping to use an API, but the Wahoo API that got published is
focused on getting and updating activities and not on monitoring the
live track. So I resorted to a very hackish way to extract the last
update time for a user's live track. First you have to configure a
permanent live track link. Then I use the Home Assistant command_line
sensor to monitor how long it has been since the last live track
update. When the update time goes below 5 minutes, I take that to mean
I am cycling. This then triggers the Quidditch state.

The command looks like this:

```
curl -s https://www.wahooligan.com/users/live/SECRET_URL | grep 'class=\"livetrack\"' | sed -E 's/.+data\\-seconds\\-since\\-update=\\\"([0-9]+)\\.[0-9]+\\\".+/\\1/'"
```

This is what goes into sensors.yaml. I keep the command in
secrets.yaml, as the URL is a secret and there is no way to mix
!secret directives into a command line action.

```yaml
  - platform: command_line
    command: !secret wahoo_command
    name: Bryn Last Actively Cycling
    unit_of_measurement: "seconds"
    command_timeout: 15
    scan_interval: 300
```

## 2023-10-01 jinja macros

Created Jinja templating macros to compute the home AP name and implement each sensor in HomeAssistant. This eliminates all the duplication of code and logic.

Note to self: update the code in this github repo.

## 2024-01-01 No More Life360

Life360 removed from HomeAssistant, because Life360 locked everyone out of their API access. 
I migrated to using the Apple iCloud integration. I added an automation that does a iCloud
update whenever someone leaves home. The iCloud integration isn't as fast or frequent with 
location updates as life360 was, nor does it give speed information. I'm considering migrating
to Traccar, but at the moment iCloud works just fine. 

# Specification

Assorted measurements and specifications for parts. Pulling this out
of the README to reduce clutter in the README.

## Clock Hand Dimensions

Clock hands dimensions:

- center-to-point: 88-92mm (so that the point does not obscure text)
- width: 12-14mm (can vary, allow room for names)
- thickness: 3mm (2mm was a little too thin)
- max thickness around center hole: 4mm

## Clockwork Dimensions

- clockwork depth: 4.125" (behind the face)
- clockwork width: 6.625"
- clockwork height: 3"
- hands depth:     2"     (with 0.125" clearance from glass)

## Clock Face Dimensions

Clock face dimensions: 
    -   width 9.75"
    -   height of square face 9.5"
    -   total height 13.5"
    -   top semi-circle indentation: 1"
    -   top semi-circle height: 4"
    -   clock face radius: 4"

## Clock Hand Ideas

This section is a collection of ideas on other ways to create custom
hands or make use of antique clock hands.

Goals
- mounting could be with 3D printing with a collet (clip)
- Something like the metallic scissors w/ engraved names
- clock hands could either be 3D printed or possibly laser cut from metal

Resources:
- https://www.bearwood.com/clock-hands-for-purchase.html
- https://www.ebay.com/str/JRCLOCKER-Watches-and-Clocks
- https://www.walnuthollow.com/store/clock-making/hands/
- https://www.cmi-hermle.com/category/40-handnuts-hand-bushes
- https://www.cmi-hermle.com/category/38-hands-mechanical
- https://www.clockworks.com/clock-parts/clock-parts.html
- https://www.mcmaster.com/flanged-bushings Flanged for mounting flat clock hands
- https://timesavers.com/c-325673-clock-repair-replacement-parts-hands-related-hand-bushings.html
- https://perrinwatchparts.com/collections/clock-hand-nuts/products/clock-parts-740191?variant=39071940047
- The clips to connect hands to the shaft are called collets
- http://www.m-p.co.uk/muk/parts/hands-collets.htm

## Clock Hands Solution

My son, Alex, generated the 3D CAD models for the hands with some
artistic input from myself. In particular I spent a fair amount of
time finding a good font to use. After a couple iterations they came
out great! He put in a little extra time to make his clock hand have
some extra flair.

I kept the production in house. My father-in-law ran the 3D printer to
print them.

Attaching them to the brass rods turned out not to be an issue at
all. The 3D hands were printed with slightly undersized holes. I filed
out the holes so that they would fit, but very securely. 

## Fonts

Here are the [fonts](fonts/Fonts.md) I evaluated for use on the hands.

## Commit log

2019-06-19 servohat control
2019-06-20 servo notes and CAD
2019-07-07 planning clock face poster mounting
2019-11-09 CAD for clockwork parts
2019-11-09 add CAD models
2019-11-09 servocity comprehensive CAD lib
2019-11-14 printable props FB
2019-11-15 homeassitant sensors
2020-04-11 data flow diagram
2020-04-12 remove servocity CAD files
2020-04-12 clock support CAD
    [Clock_Support_Front.step, Clock_Support_Front.stl, Clock_Support_Rear.step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]
2020-04-12 remove servo CAD
2020-04-12 update CAD docs
2020-04-12 CAD attribution
2020-04-12 rename CAD files
    [Clock_Servo_Support.step, Clock_Servo_Support.stl, Clock_Shaft_Support.step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]
2020-04-12 CAD pngs
2020-04-12 CAD images
2020-04-12 more motor encoders
2020-04-17 images of clock CAD
2020-04-17 full CAD images
2020-05-18 3d printed gear research
2020-05-22 link to GrabCad for CAD files
2020-06-03 email sensor for detecting cycling
2021-07-05 wahoo live track
